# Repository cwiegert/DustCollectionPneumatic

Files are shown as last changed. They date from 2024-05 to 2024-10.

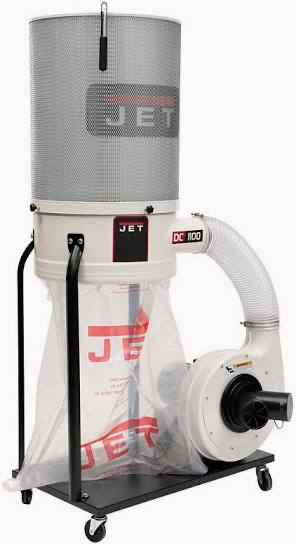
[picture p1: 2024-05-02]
DustCollection_OTA/Images/dustCollector.png

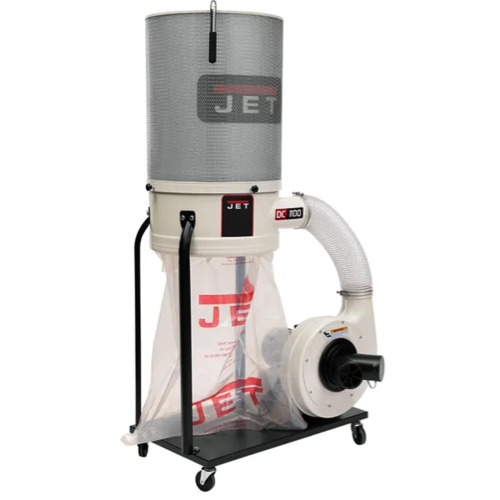
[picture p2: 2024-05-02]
DustCollection_OTA/Images/Dust Collector.jpg

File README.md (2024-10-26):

# Dust Collection Automation using Pneumatic Actuators
##  This is a next evolution of the Dust Collection EEPROM repo, with IoT and air driven gates

**IMPORTANT UPDATE V. 1.4.0 - changes to an arduino library**
Because the arduino standard install for the ArduinoMqttClient uses the MqttClient.h library, there is a 256 byte limitation on the size of messages sent to the mqtt broker.  To get around this limitation, you can modify the MQttClient.CPP found in the src directory under your standard location for the ArduinoMqttClient library install.   (typically /~/documents/arduino/library)     This repo does not contain the modified file, only the instructuions here on how to modify the buffer size for a larger topic message to the broker.   

If there is a bufffer over run, the arduino library will truncate your Json document to the size of the buffer, and NodeRed will throw an error "unexpected end of JSON file"

To modify to buffer size, open the MqttClient.cpp and chnage the parameter TX_PAYLOAD_BUFFER_SIZE

```  #ifndef TX_PAYLOAD_BUFFER_SIZE
  #ifdef __AVR__
    #define TX_PAYLOAD_BUFFER_SIZE 128
  #else
 //   #define TX_PAYLOAD_BUFFER_SIZE 256            old code which comes with the arduino library.   
    #define TX_PAYLOAD_BUFFER_SIZE 512          //  CDW 5/26/2024 because JSON messages were being truncated at 256 bytes
  #endif
#endif
```

**Why make the change from the servo driven dust gate automation?**
  
  To start with, the code base for management and administration I was looking for on the dust collection automation was getting too large to run on a single arduino.   Even with the Mega and the 8M of RAM to load programs, I had hit a limit on stability and amount of flexibility necessary for where I wanted to go with the automation.  Instead of trying to get more efficient with the 1 large code set, it was easier to go down the Internet of Things path, and have each gate be an autonomous node, but have it all wired together through NodeRed.   

  The flexibility provided by the NodeRed workflow management gave me the global orchestration necessary to configure all the gate controllers to act independently, but instruct the other nodes in the system how to operate.    The code base was going to be simpler, and there only need be a messaging system to do the instructions for system to know when to open and close a gate.   In this workflow, we also added the delay to allow for start and stop a machine (i.e. current on, off, on, off ) like a chop saw without continuously cycling the dust collector.    The *reset timer* and *store delay* functions on the Dust Collector panel control when the GPIO on the Raspberry Pi is set to off.

  Secondly, with the simplification of the nodes and code, I could run the NodeRed and the Mosquitto MQTT broker on a Raspberry Pi.   By adding the Raspberri Pi to the system and running the dust collector off a GPIO pin on the Pi, there was no need to write any code to control the logic of the collector.   Simply, there would be a NodeRed workflow which set the GPIO to high or low, all based on the logic from the outlet monitor on the gate.  

  Finally, the servo's kept burning up!   Because the gates are not precise with the slides and dust was getting into the gate slide, the servo was not powerful enough to drive the gate open/closed when there was dust in the slide, or if the slide was a little out of center.   Even with 35kg servo's, the gate would bind.  Because there is no feeback loop from the servo, it will continue to try to run to the position instructed until it either gets to that position or, the servo burns it's windings.

  Enter youtube!    I need to give an acknowledgement and shout out to Rings Workshop and this video he put out [Rings Workshop](https://www.youtube.com/watch?v=1p1USQXDALg)    YES!!!!  that is what I was looking for.   The code base is pretty simple on his set up, and follows the same pattern as on the EEPROM version from my repository -but the 3D printed brackets and air driven actuators is what was new for this set up.

**Configuring the System, with all the moving parts.   A simple overview, with details below**

  This system setup is driven by BLYNK OTA and all devices are activated off the auth code given when BLYNK activates a device.   The big mindset shift is that each time you activate a device, you are instantiating the Blynk Template.    When the wemos boots up, it is in activation mode, with only the factory firmware on it, and can be activated by adding a new device on the BLYNK mobile app.   Once the device is acitve, it will ping the BLYNK server for a new shipment, if 1 is found, it will be installed as the latest firmware on the device and reboot.    Whala, you have a new gate configured for the IoT system.

  **NodeRed** - is a IoT workflow manager that controls all of the inter-gate communication by use of MQTT messaging.   There is a screen shot below that outlines some of the flows, and a JSON package is included in the repo to import all the flows for the sytem.   Comments are included in NODERed to outline what each function does.   Connecting to the MQTT broker is set as the Server property within an MQTT message.  
 

  **Raspberry Pi** -- NodeRed and the Mosquitto MQTT broker are installed on a Raspberry Pi running the latest Raspbian OS.   There are plenty of sites outlining how to get each installed and running.    IT's important to note the IP address and port for the Mosquitto MQTT installation.   That variables *broker* and *port*  must be set in the *DustCollectorGlobals.h*  for any connectivity to the mqtt broker to work.   Also, the GPIO pin configured on the Dust Collector page, Node --> Collector Power, should have a wire connected to the 5V activator on the dust collector heavy duty relay switch.   (Same as it was in the EEPROM model, but here we are coming off the Pi instead of an arduino)
  

  **Voltaage Sensor** -- simplifying the systsem was 1 of the goals of this project.    Instead of having to monitor and sense a specific voltage change, I used a 5V relay switch sensor to simply send 5 volts to a INPUT_PULLUP pin and bring that pin to ground.   No, it's a matter of reading LOW on that pin, and not having to debounce and calculate the delta to remove noise from the system.   I used these from Amazon [Voltage Sensor](https://www.amazon.com/dp/B0B7VT46KG?psc=1&ref=ppx_yo2ov_dt_b_product_details)  as the sensors.  K1 and K2 are simply a switch relay which is normally open, and when current is applied, the NO switch is closed.   [Relay](https://www.amazon.com/gp/product/B01MCWO35P/ref=ppx_yo_dt_b_asin_title_o00_s00?ie=UTF8&psc=1) 


**12V external power supply** -- used to power the solenoid through the Wemos Relay shield.   Of course, if you are using heavier duty solenoid (24V) you will need to match the power supply to the voltage of the solenoid, and have a corresponding relay that can handle the voltage.   I typically use the MDR-60-12 by MeanWell, as I have used MeanWell on all my automation projects and have never had any issues.

**5V LED's colored** -- used to provide external indication of what is happening with the lights of the Wemos and Relay.   Have Red for when the relay is activated and voltage through NO, and Blue which is synched up to the Wemos onboard LED flashing light.   These come with an inline resistor --> [5V Colored LED](https://www.amazon.com/dp/B07TPMRLVR?psc=1&ref=ppx_yo2ov_dt_b_product_details)

**Buck Converter** -- added this to the system to manage the all the power.   The 12V line will run from teh power source, either in parallel or branched from gate to gate along a single trunk.   [Buck Converter](https://www.amazon.com/dp/B081N6WWJS?psc=1&ref=ppx_yo2ov_dt_b_product_details) the 12v, will be dropped down to 5V to run the wemos, and a line will branch off the [Splitter](https://www.amazon.com/dp/B087B6FQLB?psc=1&ref=ppx_yo2ov_dt_b_product_details) to run the solenoid (12V) and another 12V branch to power the next gate in line.

  **Soldering the Wires, and configuring the pins**
1. GPIO 12 (D6) on the Wemos  -----------  K1 on Voltage Sensor
2. K2 on voltage sensor       -----------  Ground on Wemos
3. D1 on Wemos                -----------  Default driver for the Wemos Relay (gatePin)
4. D4 on Wemos                -----------  Positive leg of Blue LED (external flasher of the onboard LED)
5. Negative leg of LED        -----------  Ground on Wemos
6. D1 on Wemos                -----------  Positive leg of Red LED (external light to show relay activated)
7. V+ on Solenoid             -----------  NO on Wemos Relay
8. V- on Solenoid             -----------  V- on 12V power supply
9. V+ on 12V power            -----------  COM on Wemos relay shield
10. Negative Leg of LED       -----------  Grown on Wemos
11. 11. USB-C power pigtail   -----------  Powers Wemos

## How this set up works ##

1.  Everything is run on a WEMOS D1 Mini with a Relay shield attached.   I prefer to use the new WEMOS, becuase the USB-C power plug is on the top of the board, and gives a better set in the box.    There are so many on Amanzon, I found [WEMOS](https://www.amazon.com/gp/product/B0BKSKV54X/ref=ppx_yo_dt_b_asin_title_o00_s00?ie=UTF8&th=1) to be easiest and most consitent 

Along with the [Relay Shields]( https://www.amazon.com/dp/B093LC9DNJ?psc=1&ref=ppx_yo2ov_dt_b_product_details)  Each gate has the logic controller and the switching mechanism to drive the air actuator.  

2.  The Air actuator is the key to this.   It is activated by the NO pole on the relay, which in turn is driven by pin **D1** on the WeMOS.  When soldering the headers to the Wemos and the relay, be sure to have the D1 and Power pins aligned or none of this system will work.     Simply, 12V power is driven to the **COM** on the relay, 1 wire from the actuator solenoid is connected to **NO** and the other solenoid wire connected to V- on the 12V power source.    The 5V trigger for the relay is pin D1, which is GPIO 5, and defined in DustCollectorGlobals.h.    I used 12V solenoids, as there isn't a need to have massive 24V drivers on these gates.... the gates are light.   I found these [Actuators]( https://www.amazon.com/dp/B00YCWL9I4?psc=1&ref=ppx_yo2ov_dt_b_product_details) to fit the hangers best.


3.  The solenoids drive the air piston.   They are fairly inexpensive and can be found again on Amazon [Solenoids]( https://www.amazon.com/dp/B07DYPM7XB?ref=ppx_yo2ov_dt_b_product_details&th=1)    The air piston is connected to the gate via the 3D printed connecting arm.   The links to all the 3D printed parts can be found at the bottom of the readme, and all the .STL's and fusion360 files are in the repo.

4.  It's really simple.    The wemos starts up and activates itself, waiting for a configuration.   Start the "add new device" from the Blynk App and discover the new wemos.   The firmware is updated and the wemos reboots.   Upon reboot, the 2.4Ghz network you set during the activation will be used to reconnect to you network.  NO credentials are stored in discoverable format.   Once up and running, the wemos will send it's gate ID to the NodeRed, which will add the id to the global array, or if not unique, will hand you back a gate id which is then stored in EEPROM on the wemos.
   
5.  Configure the gate map on the BlynkApp.    **IMPORTANT** The gateMap array is a 0 based array, and typically a system is set up with the first gate in being gateID #1.   Remember to put a 0 placeholder in all your gateMaps, or the array for each gate will be out of synch.  So if you have 6 gates, you will need 7 elements in the array "0110001".   If your tool is on gate 6, the map will open gates 1, 2 and 6 will be the activation gate.   The leading 0 is not used, but is necessary.  This will be a critical step if you have gates to open between your machine driven gate and the dust collector.   It's very simple, each position in the 0-1 map corresponds to an index of a gate.   If there is a 1, the gate should be opened, if closed, a 0.   Save the new name, tool name, gate map to EEPROM, and restart the device.    You're ready to go.

6.  The code is really really simple.   The readOutlet function is run in the Loop.   That function simply checks the outletPin for a pull down to LOW.   If low, it tells NodeRed a tool has been turned on, NodeRed then tells all gates to run the gate map it sends as part of the JSON message.  Every gate, except the 1 originating the message, will either open or close itself.

7.  If a gatePin is read LOW, and the "isOn" flag is set, the spin down timer is reset to 0, and the next outlet is checked.
  
9.  If there is no machine running, the spin down value will be applied, a message to close all gates and spin down the dust collector is issued...

**Assembly of 3D printed parts**
For simplicity sakes, there have been heated threaded inserts added to this model.   In previous versions, there were threaded holes in the PETG, but the risk of stripping the treads and the screws cross threading made the assembly of the parts difficut.     The buck converter box is connected to the hanger with M2 insters, while the air solenoid and the wire connector/splitter use M3.    To install, use the provided soldering iron tip, heat the soldering iron to 300 C, slip the insert onto the tip and melt it into the pre-printed holes.    

Parts are found in the links section below.

M2  

M3


______________________________________________________________________________________________________
**Links**

[3D files](https://www.thingiverse.com/thing:6603995)    other than in this git repo

[Solenoids](https://www.amazon.com/dp/B07DYPM7XB?ref=ppx_yo2ov_dt_b_product_details&th=1)

[Actuators]( https://www.amazon.com/dp/B00YCWL9I4?psc=1&ref=ppx_yo2ov_dt_b_product_details)

[WEMOS D1 Mini](https://www.amazon.com/gp/product/B0BKSKV54X/ref=ppx_yo_dt_b_asin_title_o00_s00?ie=UTF8&th=1)

[WEMOS Relay 12V, 5V activation]( https://www.amazon.com/dp/B093LC9DNJ?psc=1&ref=ppx_yo2ov_dt_b_product_details)

[LEDs](https://www.amazon.com/dp/B07TPMRLVR?psc=1&ref=ppx_yo2ov_dt_b_product_details)

[USB Pigtails](https://www.amazon.com/dp/B0CMQ2SYF3?psc=1&ref=ppx_yo2ov_dt_b_product_details)

[MiniPlug pigtail](https://www.amazon.com/dp/B0B4C2VSHV?psc=1&ref=ppx_yo2ov_dt_b_product_details)

[Current Sensing Relay](https://www.amazon.com/dp/B0B7VT46KG?psc=1&ref=ppx_yo2ov_dt_b_product_details)

[Long screw for box top](https://www.amazon.com/dp/B09LYKYV2S?psc=1&ref=ppx_yo2ov_dt_b_product_details)

[Screw for box top](https://www.amazon.com/dp/B07H14FRRB?psc=1&ref=ppx_yo2ov_dt_b_product_details)

[M3 screws for holding solenoid](https://www.amazon.com/dp/B0CMDHGNJF?psc=1&ref=ppx_yo2ov_dt_b_product_details)

[CF-PETG](https://www.amazon.com/dp/B0CCVKJJQC?psc=1&ref=ppx_yo2ov_dt_b_product_details)

[Air fittings](https://www.amazon.com/dp/B07ZHG8Y1Y?psc=1&ref=ppx_yo2ov_dt_b_product_details)

[Air mufflers](https://www.amazon.com/dp/B08K6T9H2K?psc=1&ref=ppx_yo2ov_dt_b_product_details)

[Air Controller](https://www.amazon.com/dp/B01ILJFJ4I?psc=1&ref=ppx_yo2ov_dt_b_product_details)

[12V - 5V Buck Convert](https://www.amazon.com/dp/B081N6WWJS?psc=1&ref=ppx_yo2ov_dt_b_product_details)

[Wire Connector and Splitter](https://www.amazon.com/dp/B087B6FQLB?psc=1&ref=ppx_yo2ov_dt_b_product_details)

[M3 heated insert](https://www.amazon.com/dp/B0BBSLL6G7?ref=ppx_yo2ov_dt_b_product_details&th=1)

[M2 heated insert](https://www.amazon.com/dp/B0CS6XJSSL?ref=ppx_yo2ov_dt_b_product_details&th=1)

[Raspberry Pi case](https://www.amazon.com/dp/B08VSDCQM2?psc=1&ref=ppx_yo2ov_dt_b_product_details)

[Raspberry Pi monitor](https://www.amazon.com/dp/B0153R2A9I?psc=1&ref=ppx_yo2ov_dt_b_product_details)

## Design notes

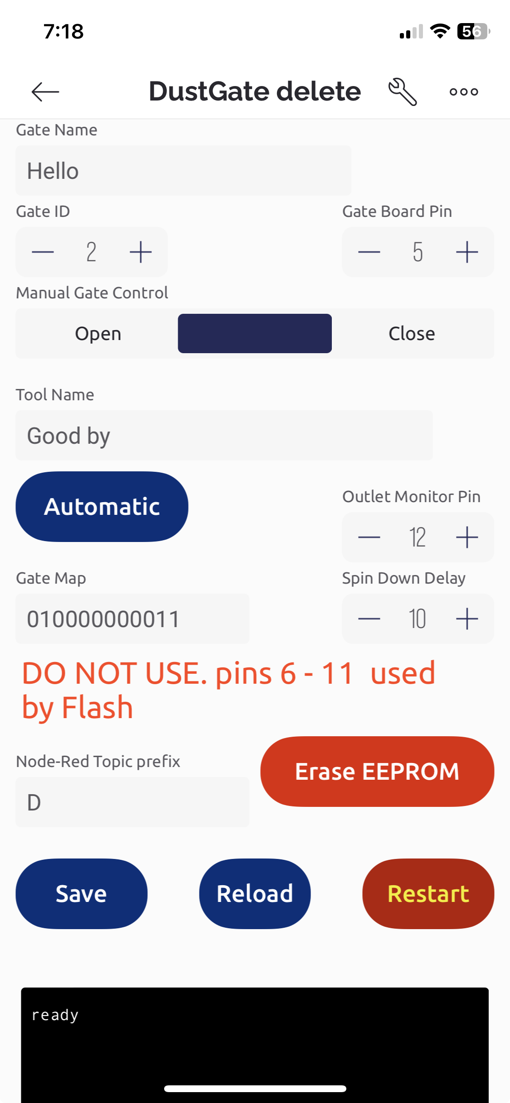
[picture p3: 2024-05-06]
DustCollection_OTA/Images/Dust collection OTA Blynk App.jpeg

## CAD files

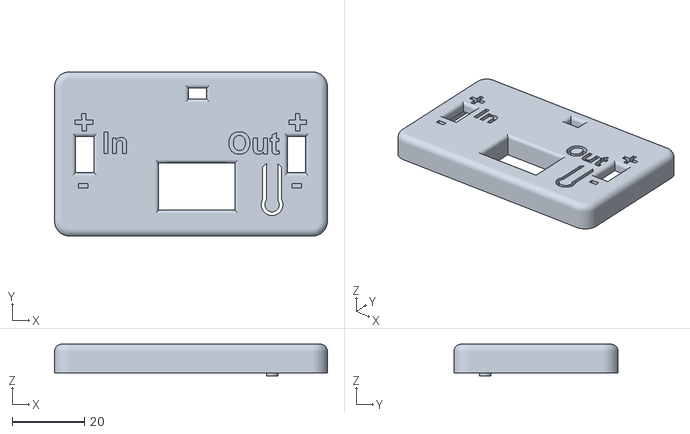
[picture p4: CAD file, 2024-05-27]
DustCollection_OTA/3 D printing files/Buck Converter Box Top.stl
75.4 x 45.4 x 8.75

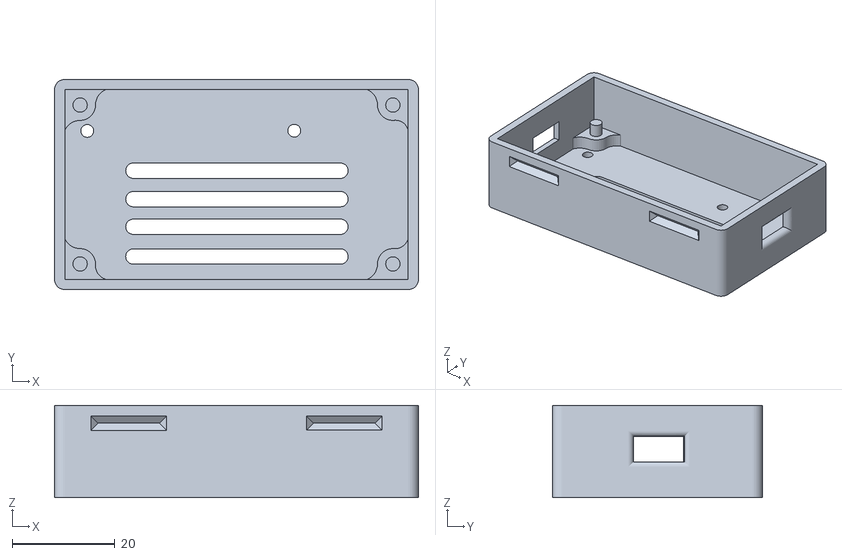
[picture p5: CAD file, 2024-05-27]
DustCollection_OTA/3 D printing files/Buck Converter Box LM2596S.stl
71.0 x 41.0 x 18.0

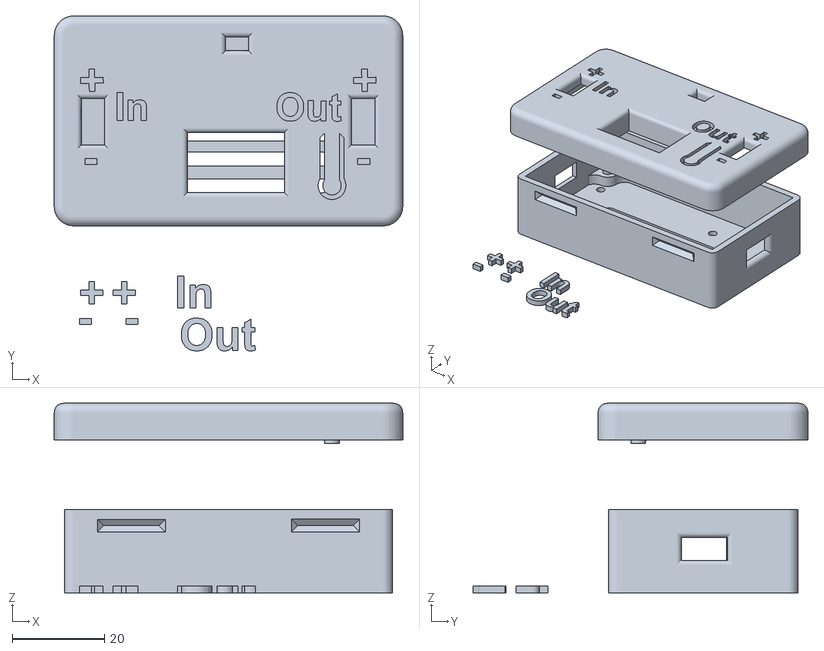
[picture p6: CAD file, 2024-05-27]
DustCollection_OTA/3 D printing files/Buck Converter case v16.stl
75.4 x 72.5 x 41.0

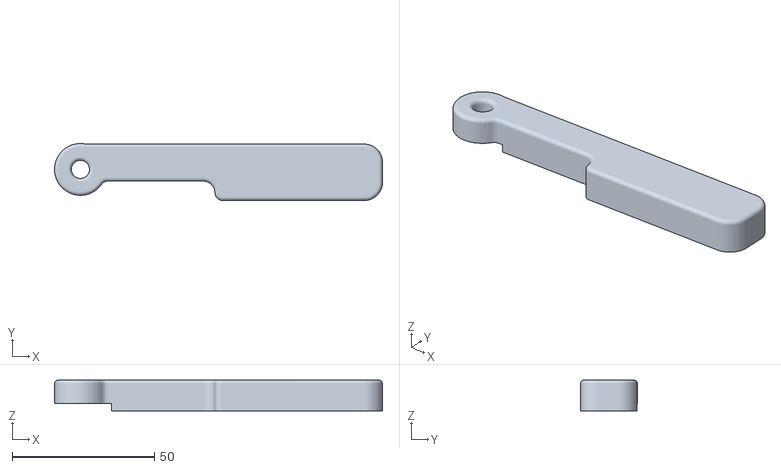
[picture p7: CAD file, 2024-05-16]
DustCollection_OTA/3 D printing files/gate connection bracket - threaded not through.stl
115.2 x 20.0 x 10.8

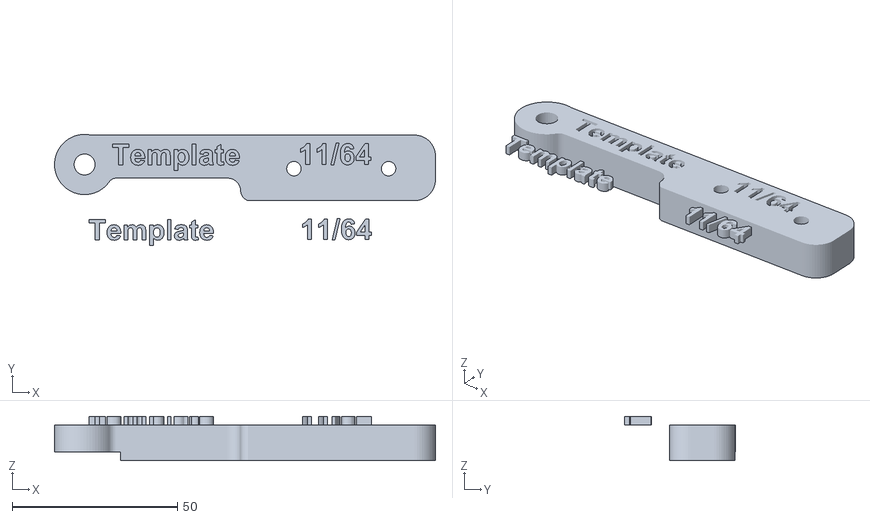
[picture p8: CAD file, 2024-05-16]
DustCollection_OTA/3 D printing files/gate connection bracket - through template.stl
115.2 x 33.6 x 13.3

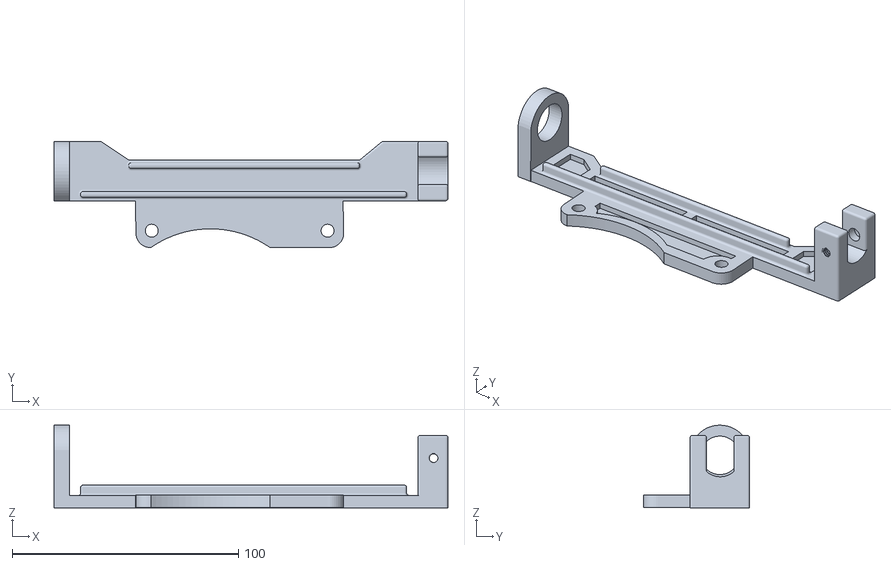
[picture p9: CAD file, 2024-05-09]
DustCollection_OTA/3 D printing files/Air Actuator gate bracket.stl
174.0 x 46.9 x 36.5

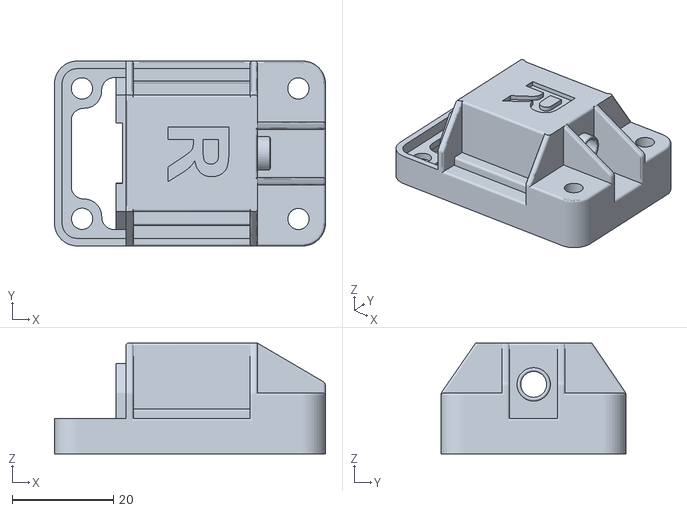
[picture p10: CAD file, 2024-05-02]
DustCollection_OTA/3 D printing files/Top of Box.stl
53.5 x 36.5 x 21.9

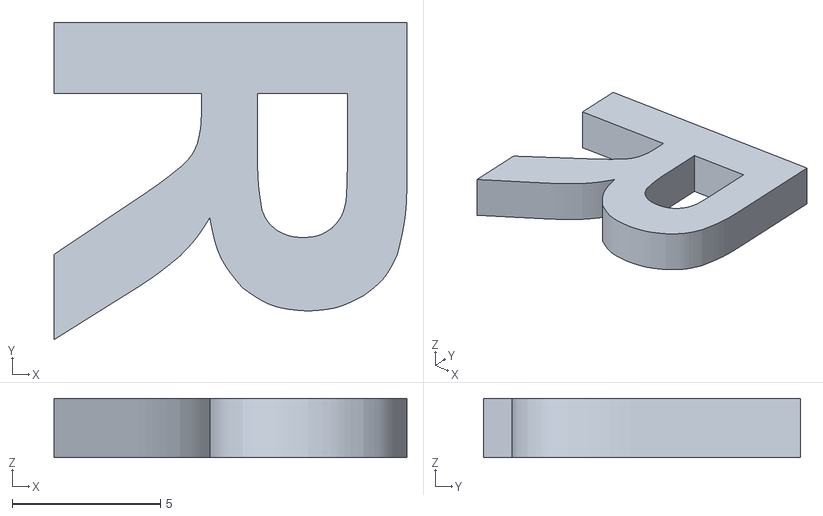
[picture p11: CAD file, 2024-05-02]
DustCollection_OTA/3 D printing files/R for top of Box.stl
11.9 x 10.7 x 2.00

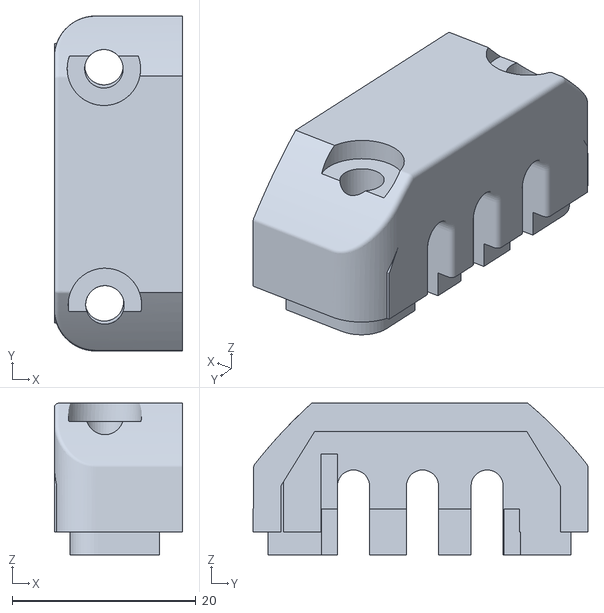
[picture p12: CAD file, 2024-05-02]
DustCollection_OTA/3 D printing files/Front Cap.stl
14.0 x 36.5 x 16.5

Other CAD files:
DustCollection_OTA/3 D printing files/4 inch gate connection bracket - threaded not through.stl
DustCollection_OTA/Fusion 360 Files/4 inch gate connection bracket - threaded not through.f3d
DustCollection_OTA/Fusion 360 Files/4 inch gate connection bracket - through template.f3d
DustCollection_OTA/Fusion 360 Files/Buck Converter case v16.f3d
DustCollection_OTA/Fusion 360 Files/gate connection bracket - threaded not through.f3d

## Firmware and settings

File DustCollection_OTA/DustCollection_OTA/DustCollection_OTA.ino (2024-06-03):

/*************************************************************
  Blynk is a platform with iOS and Android apps to control
  ESP32, Arduino, Raspberry Pi and the likes over the Internet.
  You can easily build mobile and web interfaces for any
  projects by simply dragging and dropping widgets.

    Downloads, docs, tutorials: https://www.blynk.io
    Sketch generator:           https://examples.blynk.cc
    Blynk community:            https://community.blynk.cc
    Follow us:                  https://www.fb.com/blynkapp
                                https://twitter.com/blynk_app

  Blynk library is licensed under MIT license
 *************************************************************
  Blynk.Edgent implements:
  - Blynk.Inject - Dynamic WiFi credentials provisioning
  - Blynk.Air    - Over The Air firmware updates
  - *************************************************************/


/**************************************************************************************
 *  DustCollection_OTA 
 * 
 *  Author:   Cory D. Wiegert
 *  Date:     April, 7, 2024
 *  License:  all code open source and licensed under MIT license 
 *  
 * 
 * Background:
 *              New version of dust collection automation.   In previous versions, found here
 *              https://github.com/cwiegert/DustCollectionEEPROM all the gates were controled via
 *              software running on an Arduino Mega, with the configuration all managed in a single place.
 *              This version, is an IOT model, where all the code for each gate is managed on a NodeMCU
 *              and synched to a NODE-RED instance running on a raspbery PI.   The communications are 
 *              over the MQTT connecting to a mosquitto broker running on the same raspberry pi.
 *              The gates are managed with air actuators, and a single HIGH/LOW to the 12v relay to trigger the
 *              air solenoid.
 * 
 *              All activation of the NodeMCU's are done through Blink OTA, and upgrades destributed through the BLYNK update 
 *              package and the BLYNK_FIRMWARE_VERSION attribute below.   To updrage the NodeMCU's, simply increment the version
 *              and create the publication package on the BLYNK developer screen.   
 * Libraries:
 *          - Blynkedgenet.h                      incstalled via the Arduino Library Manager
 *          - BlynkSimpleShieldESP3266.h          installed via the Blynk library in Arduino Library Manager
 *          - ArduinoJson.h                       installed via the Arduino Library Manager
 *          - ArduinoMqttClient.h                 installed via the arduino Library Manager
 *          - DustCollectorGlobals.h              manually built and in the library directory of the git repo
 *        
 * version:
 *     4/07/2024  CDW   1.1.0 -- plugged into NODE-RED, skipping the outlet with a 0 as the outlet pin
 *     4/27/2024  CDW   1.3.0 -- implemented V0 to erase EEPROM, did null checks on BLYNK UI, set them to constants when null
 *     4/27/2024  CDW   1.3.3 -- updated the gate pin to hard default to GPIO 5 or pin D1 on teh WEMOS D1 
 *     5/6/2024   CDW   1.3.4 -- publish to GitHub under new repository
 *     5/17/2024  CDW   1.3.5 -- added the chip id as part of the blast gate structure.   Will use this in NodeRed for maintaining gate ID
 *     5/26/2024  CDW   1.3.6 -- changed the gate map for loop, instead of temp+1 < string, it's just temp < strlng
 *     5/26/2024  CDW   1.4.0 -- MAJOR change to the MqttClient.cpp library from the Arduino client library.   Changed the TX_PAYLOAD_BUFFER_SIZE 512 from 256
 *                               The Mqtt JSON messages were being truncated at 256 (default for the payload buffer).   Will need to package this library with the git, or 
 *                               make sure to call out in the readme.   Have highlighted in the CPP code
 *     
 * 
*********************************************************************************************************************/

/* Fill in information from your Blynk Template here */
/* Read more: https://bit.ly/BlynkInject */
#define BLYNK_TEMPLATE_ID "TMPL24bXLC68L"
#define BLYNK_TEMPLATE_NAME "Blynk Provision"

#define BLYNK_FIRMWARE_VERSION "1.4.0"  

#define BLYNK_PRINT Serial
//#define BLYNK_DEBUG

#define APP_DEBUG

// Uncomment your board, or configure a custom board in Settings.h
//#define USE_SPARKFUN_BLYNK_BOARD
#define USE_NODE_MCU_BOARD
//#define USE_WITTY_CLOUD_BOARD
//#define USE_WEMOS_D1_MINI

#include "library/BlynkEdgent.h"
#include "library/DustCollecterGlobals.h"


WidgetTerminal  statusUpdate(V17);        // terminal on the mobile app to update status

BLYNK_WRITE (V0)  // ERASE EEPROM clearing it from old configuration   1.3.0
  {
    if (param.asInt())
      {
        saveConfigEEPROM (E_ERASE);
      }
  }

BLYNK_WRITE(V2)  // gate control pin from the blynk Config Screen
{
  blastGate.gatePin = param.asInt();
  dirtyConfigBit = true;
}

BLYNK_WRITE(V3)  // collector spin down delay, from Blynk config screen
{
  blastGate.collectorDelay = param.asInt();
  dirtyConfigBit = true;
}

BLYNK_WRITE(V4)  // outlet pin, if button is not set to digital, from Blynk config screen
{
  blastGate.outletPin = param.asInt();
  dirtyConfigBit = true;
}

BLYNK_WRITE(V6)  // gate name from the Blynk Config Screen
{
  strcpy(blastGate.gateName, param.asStr());
  dirtyConfigBit = true;
}

BLYNK_WRITE(V5)  // gate id from then Blynk Config Screen
{
 
  holderGateId = blastGate.gateID;
  blastGate.gateID = param.asInt();
  dirtyConfigBit = true;
  changeGate = true;

}

BLYNK_WRITE(V9)   //  multi-selector to either open or close gate
  {
    if (param.asInt() == 0)
      openGate();
    else if (param.asInt() == 2)
      closeGate();
    Blynk.virtualWrite(V9, 1);
  }

BLYNK_WRITE(V11)  // tool name from the Blynk Config Screen
{
  strcpy(blastGate.toolName, param.asStr());
  dirtyConfigBit = true;
}

BLYNK_WRITE(V12)  // node-red prefex - not implemented yet
  {
  strcpy(blastGate.nodeRedPrefix, param.asStr());
  dirtyConfigBit = true;
  }

BLYNK_WRITE(V13)  // gate map from the Blynk config Screen
{
  strcpy(blastGate.gateMap, param.asStr());
  //Serial.println(blastGate.gateMap);
  dirtyConfigBit = true;
}

BLYNK_WRITE(V14)  // Save to EEPROM button
{ 
  if (param.asInt() == 1)
    {    
      DynamicJsonDocument jSonDoc(JSON_SIZE);
      String mapToJson;
      statusUpdate.clear();
      if (dirtyConfigBit == true )
        {  
          if (changeGate == false)
            {
              saveConfigEEPROM(E_WRITE);
              dirtyConfigBit = false;
            }
          else
            {
              if (blastGate.gateID != holderGateId)     // gate ID has changed, and need to remove the old gate from the parameter array
                {       
                  jSonDoc["gate Id"] = blastGate.gateID;
                  jSonDoc["holder"] = holderGateId;
                  serializeJsonPretty (jSonDoc, mapToJson);
                  
                  if (!mqttClient.connected())
                    mqttClient.connect(broker, port);
                  mqttClient.beginMessage (REGISTER);       
                  mqttClient.println (mapToJson);
                  mqttClient.endMessage(); 
                } 
            }
        }
    }  
}

BLYNK_WRITE(V15)  // Refresh from EEPROM
  {
  if (param.asInt() == 1 )
    if (getEEPROMConfig(15))
      setBlynkConfigUI();
  }

BLYNK_WRITE(V16)  // red button on screen to reset the board
  {
    if (param.asInt())
      ESP.restart();
  }

BLYNK_WRITE (V17)
  {
    // if I want input from the Blynk screen I would write it here
  }

/************************************************************
 * void runOutletCheck()
 *    check to see if the pin being monitored for for a voltage changed
 *    has been bit flipped to HIGH.   If so, call the gate map map function
 *    set the JSON object with the gate map in each of the elements, which is 
 *    then broadcast to all the gates to set their appropriate state.
 * 
**********************************************************************/
void runOutletCheck() 
  {

    String mapToJson;
    DynamicJsonDocument jSonDoc(JSON_SIZE);

    if (blastGate.outletPin > 0)                  // skip the outlets that aren't connected to an outlet
      {
        jSonDoc["sent Gate"] = blastGate.gateID;
        jSonDoc["outlet"] = blastGate.outLetDigital;
        jSonDoc["spinDown"] = blastGate.collectorDelay;
        jSonDoc["machine"] = blastGate.toolName;

        JsonObject gateMap = jSonDoc.createNestedObject("gateMap");
        int temp = 0;
        do
        {
          gateMap[String(temp)] = blastGate.gateMap[temp] - '0';          // create the nested JSON object with the gate states set 1 per element ()  1.3.6
          temp++;
        } while (blastGate.gateMap[temp] != '\0' && temp < 32);
           
        serializeJsonPretty(jSonDoc, mapToJson);
        //serializeJsonPretty(jSonDoc, Serial);
        if (!mqttClient.connected())    // check for a disconnect and reconnect to make sure messages go through
          mqttClient.connect(broker, port);
     // Serial.println("toolIsOn value ==> " + String (toolIsOn) + " pn  ==> " +  String(blastGate.outletPin )+ "==> "+ String(digitalRead (blastGate.outletPin)));
        if (toolIsOn == false)
          {
            if (digitalRead (blastGate.outletPin) == LOW)      // current flowing through the INPUT_PULLUP, going to ground pulls to LOW
              {
                digitalWrite(blastGate.gatePin, HIGH);        // send send 5V to the gate pin, signal relay to open gate
                digitalWrite(1, HIGH);
               
                mqttClient.beginMessage(TOOL_ON);
                mqttClient.println(mapToJson);
                mqttClient.endMessage();                      // Call Node-Red and turn the collector on, Node-red will run gate maps as a TOPIC back to all gates
                toolIsOn = true;
              }
          }
        else 
          {
            if (digitalRead(blastGate.outletPin) == HIGH && toolIsOn == true)       // tool has been running and is now turned off INPUT_PULLUP hold HIGH when no outside current
              {
                //Serial.println("I tiggered the HIGH condition on readOutlets");
                     // set the 
                mqttClient.beginMessage(TOOL_OFF);            // Turn tool off if elapsed time > delay spin down
                mqttClient.println(mapToJson);
                mqttClient.endMessage();
              }
            else if (toolIsOn == true)
              {
                if (!mqttClient.connected())    // check for a disconnect and reconnect to make sure messages go through
                  mqttClient.connect(broker, port);
          
                mqttClient.beginMessage (TOOL_RESET);         // Need to reset the elapsed time timer, and don't want to run through the startup in NodeRed
                mqttClient.println(mapToJson);
                mqttClient.endMessage (); 
              }
          }
      }
  }

/***********************************************************
 *  void nodRedListenCallback (int _size)
 *      callback function for all the node red topic handling
 * ************************************************************/
void nodeRedListenCallback ( int _size)
  {
    int workingGate;
    int __gateState;
    char  payload[_size + 1];
    String topic;
    //int error = 0;
    
    //DynamicJsonDocument jSonDoc(JSON_SIZE);
   DynamicJsonDocument jSonDoc(512);
    topic = mqttClient.messageTopic();
      if (topic != GATE_ID_SEND && topic != CLOSE_ME)    // check the topic to make sure there is a json document
    {     
      mqttClient.readBytes (payload, _size);           // read the incoming message
      payload[_size+1] = '\0'; 
      DeserializationError error=deserializeJson (jSonDoc, payload);       //deserialize the incoming payload to a json document
      if (error) 
        {
          Serial.print(F("JSON parsing error: "));
          Serial.println(error.c_str());
          return;
        } 
    }

     if (topic == GATE_ID_SEND)           // if Node-red has asked this gate to publish the ID
      {
        String mapToJson;
        jSonDoc["gate chip id"] = blastGate.wemos_id;     // 1.3.5 added the wemos_id to use in the check for unique and clearing the array
        jSonDoc["gate_ID"] = blastGate.gateID;
        jSonDoc["gate Name"] = blastGate.gateName;
        serializeJsonPretty (jSonDoc, mapToJson);
    //    serializeJsonPretty (jSonDoc, Serial);
        mqttClient.beginMessage (PUBLISH_GATE_ID);
        mqttClient.println (mapToJson);
        mqttClient.endMessage();
      }
    else if (topic == RUN_GATES)          //  get the value from the gateMap, open or close gaet base on gateMap 
      {
          mqttClient.readBytes (payload, _size);
        
          payload[_size] = '\0';
          DynamicJsonDocument  mqttDoc (JSON_SIZE);
          
          deserializeJson (mqttDoc, payload);
        //  serializeJsonPretty (mqttDoc, Serial);
          workingGate = mqttDoc["sent Gate"];
          String bgString = String(workingGate);
          String _gate = String(blastGate.gateID);
          JsonObject gateMapObject = mqttDoc["gateMap"].as<JsonObject>();;
          
          if (workingGate != blastGate.gateID)    // so long as this code is not running on the instructing gate, execute gate action
            {
              __gateState = gateMapObject[_gate];
              if (__gateState == LOW)
                closeGate();    
              else 
                openGate();           
            }
      }
    else if (topic == CLEAR_NODES)       // Not Implemented yet
      {

      }
    else if (topic == NOT_UNIQUE)
      {
        blastGate.gateID = jSonDoc["gate Id"];
        if (saveConfigEEPROM(E_WRITE))
          {
            Blynk.virtualWrite (V5, blastGate.gateID);
            Blynk.syncVirtual (V5);
            holderGateId = -1;
            dirtyConfigBit = false;
            statusUpdate.clear();
            statusUpdate.print ("changed the gate Id to ==> " );
            statusUpdate.println (blastGate.gateID);
            statusUpdate.println (F("be sure to check the gate map for the appropriate mapping to the gate"));

          }
      }
    else if (topic == IS_UNIQUE)         //  implement the save to saveConfigEERPOM here, only if a unique value comes back from node-red
      {
        if (saveConfigEEPROM(E_WRITE))
          {
            holderGateId = -1;
            dirtyConfigBit = false;
          }
        
      }
 
    else if (topic == CONFIRM_OFF)         // resets the toolIsOn variable
      {
          toolIsOn = false;
          mqttClient.beginMessage(CLOSE_ALL);    // want to close all the gates, so the relays are not always energized
          mqttClient.endMessage ();

      }
    else if (topic == CONFIRM_ON)
      {
        mqttClient.readBytes (payload, _size);
        
          payload[_size] = '\0';
          DynamicJsonDocument  mqttDoc (JSON_SIZE);
          
          deserializeJson (mqttDoc, payload);
           //serializeJsonPretty (mqttDoc, Serial);
          workingGate = mqttDoc["sent Gate"];
   // Serial.println ("blastGate.gateId ==> " + String (blastGate.gateID) + " | workingGate ==> " + String (workingGate));
          if (workingGate == blastGate.gateID)    // only turn the tool on if this gate turned on the collector
            toolIsOn = true;
      }
    else if (topic == CLOSE_ME)
        {
           closeGate();                           // all gates will close, including the "was on " tool gate
        }
    else if (topic == TOOL_ON)          // Not Implemented yet
      {

      }       
    else if (topic = NEW_GATE_ID)       // Not implemented yet
          {
            // or do i put the logic for the calling of node-red here, and let the IS-UNIQUE handle the response from mqtt
          }     
  }

void setMQttSubscriptions()                 // function to define which topics are subscribed, and setting the callback
  {
      mqttClient.subscribe (RUN_GATES); 
    //mqttClient.subscribe (CLEAR_NODES);
    mqttClient.subscribe (GATE_ID_SEND);
    //mqttClient.subscribe (PUBLISH_GATE_ID);
    mqttClient.subscribe (NOT_UNIQUE );
    mqttClient.subscribe (IS_UNIQUE );
    mqttClient.subscribe(CONFIRM_OFF);
    mqttClient.subscribe(CONFIRM_ON);
    mqttClient.subscribe(CLOSE_ME);
   // mqttClient.subscribe (NEW_GATE_ID);
    mqttClient.onMessage (nodeRedListenCallback);
   }

/*******************************************************************
 * bool saveConfigEEPROM()
 *    used from teh blynkUI to save any changes in the gate configuration 
 *    screen.   Will only write if the dirty_bit has been set to true
 *    returns false if not able to save to eeprom
**********************************************************************/
bool saveConfigEEPROM( int _RW)             // checks for WRITE or ERASE and saves blastGate structure to EEPROM or erases EEPROM
  {

    int remaining;
    remaining = EEPROM.length() - sizeof(configStore) - sizeof(blastGate);
    if (remaining > 0 && _RW == E_WRITE)
      EEPROM.put (configAddy, blastGate);
    else if (_RW == E_WRITE)
    {
      Serial.println(F(" the blast gate structure will not fit in EEPROM"));
      return false;
    }
  //Serial.println("dirtyConfig ==> " + String(dirtyConfigBit) + " | remaining ==> " + String (remaining) + " | __RW ==> " + String(_RW));
    if (dirtyConfigBit && remaining > 0 && _RW == E_WRITE) 
      {
        
        EEPROM.put(configAddy, blastGate);
        EEPROM.commit();
        Serial.println(F("WROTE blast gate structure to EEPROM"));
        dirtyConfigBit = false;
        statusUpdate.println (F("saved new settings to EEPROM"));
        return true;
      } 
    else if (_RW == E_ERASE)
      {   
        int  _address = configAddy;
        int __step = 0;
        statusUpdate.clear();
        statusUpdate.print("Clearing");
        while (__step < sizeof (blastGate))
          {
            EEPROM.write(_address, 0XFF);
            _address++;
            __step++;
            statusUpdate.print(".");           // 1.3.1
          }
        //statusUpdate.clear();
        statusUpdate.println(F("\nCleared EEPROM"));
        return true;
      }
    else
      return false;
  }

bool getEEPROMConfig( int _where)            // populates the blast gate structure from EEPROM
  {
    byte temp;
    temp = EEPROM.read (configAddy);
    EEPROM.get(configAddy, blastGate);
    if (blastGate.gateID != -1 )
      return true;
    else if (_where != 15)
      {
        Serial.println(F("did not read EEPROM"));
        return false;
      }
    else
      return true;
    
  }

/**********************************************
void setPins ()
  used to set the hardware pins to the appropriate mode.   For the NODE MCU 8266
  DO NOT USE pins 6 - 11, as htey are used by the flash memory.   Since this device
  is running only a single blast gate, there shouldn't be an issue
******************************************************/

/************************************************
 * void setPins()
 *    setting the reading and the writing pins.   
 *    The outlet pin is an INPUT_PULLUP as we will be monitoring for 
 *    a change from LOW to HIGH, and the gate pin is a straight forward
 *    digital output to trigger the air solenoid
****************************************************/
void setPins()            
  {
  
    if (blastGate.gatePin < 1)
      blastGate.gatePin = GATE_PIN;
    pinMode(blastGate.gatePin, OUTPUT);
    if (blastGate.outletPin > 5 && blastGate.outletPin < 11)                    // on a WEMOS, can not use GPIO 6-11, they are used by the board directly
      blastGate.outletPin = OUTLET_PIN;  
    pinMode(blastGate.outletPin, INPUT_PULLUP);
    digitalWrite (blastGate.gatePin, LOW);          // closing the gate on startup
    pinMode(EXTERNAL_LED, OUTPUT);
    digitalWrite(EXTERNAL_LED, LOW);
  }
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
void loop() 
  {
  
    // to avoid having delays in loop, we'll use the strategy from BlinkWithoutDelay
    // see: File -> Examples -> 02.Digital -> BlinkWithoutDelay for more info
    unsigned long currentMillis = millis();
   
    if (currentMillis - previousMillis >= interval) 
      {
          // save the last time you blinked the LED
          previousMillis = currentMillis;
          BlynkEdgent.run();
          if (!mqttClient.connected())
            mqttClient.connect(broker, port);
          mqttClient.poll();
          runOutletCheck(); 
        }
  }

/*********************************************************************************************************
 * *******************************************************************************************************
**********************************************************************************************************/

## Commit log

2024-05-02 Initial creation of repo
    [Front Cap.stl, R for top of Box.stl, Top of Box.stl]
2024-05-06 Updated NodeRed flows
    also added the gate connection bracket to the 3D files
    [4 inch gate connection bracket - threaded not through.f3d, 4 inch gate connection bracket - threaded not through.stl]
2024-05-09 updated the 3D printing files
    [Air Actuator gate bracket.stl]
2024-05-16 added updated 3D printing files
    [4 inch gate connection bracket - threaded not through.f3d, 4 inch gate connection bracket - through template.f3d, gate connection bracket - threaded not throug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]
2024-05-27 V. 1.4.0
    Updated the mqtt client buffer to 512 bytes, changed the loop for the gate map to a do/while, updated NodeRed flows, added the chip ID to the JSon topic when triggering tool_on,
2024-05-27 added buck converter case
    [Buck Converter case v16.f3d, Buck Converter case v16.stl]
2024-05-27 created individual prints for loading to thingiverse
    [Buck Converter Box LM2596S.stl, Buck Converter Box Top.stl]
2024-06-03 Updated NodeRed flows
